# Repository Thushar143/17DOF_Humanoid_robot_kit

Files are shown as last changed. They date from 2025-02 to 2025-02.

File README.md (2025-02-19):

# README

## ROS2 Package

The `humanoid_description` ROS2 package was generated using the [`fusion2urdf-ros2`](https://github.com/dheena2k2/fusion2urdf-ros2) script.

### Important Notice
There are some errors in the script. Please ensure you rectify them as suggested [here](https://github.com/dheena2k2/fusion2urdf-ros2/pull/6/commits/3295ff1138d34191cdca01d7e633e04434cfb0c4) before running the Powershell commands to avoid issues in the package generation process.

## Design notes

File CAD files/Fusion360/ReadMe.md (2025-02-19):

# Important
## You should simplify the assembly before running the script.
To know how to simplify the assembly in Fusion refer to this [video](https://youtu.be/o7w7yv-Nros?t=3376).

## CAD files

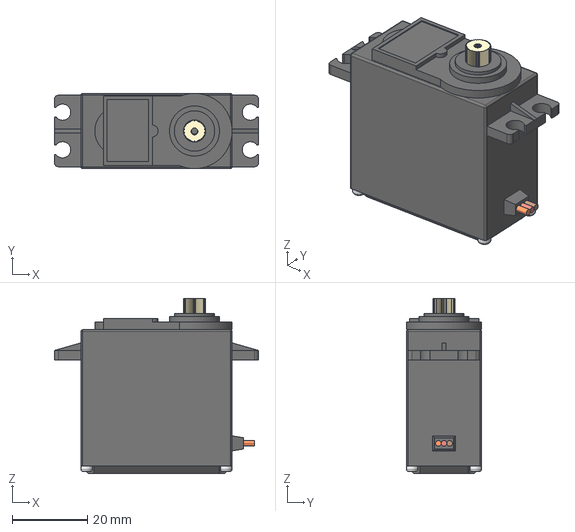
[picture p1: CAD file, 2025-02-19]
CAD files/Solidworks/MG996R.step
54.2 x 20.0 x 46.5 mm

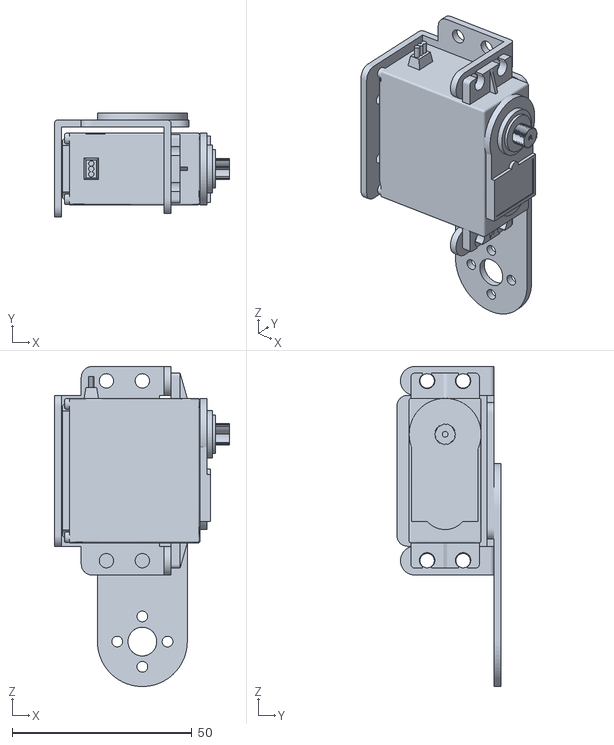
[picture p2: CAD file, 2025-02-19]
humanoid_description/meshes/L_forearm_1.stl
48.8 x 29.0 x 89.0

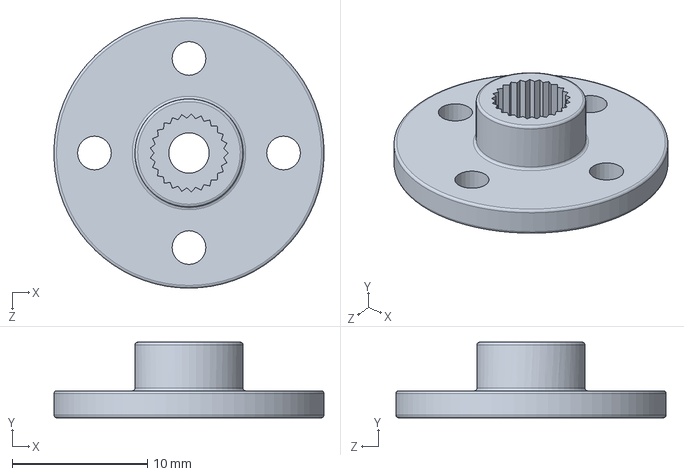
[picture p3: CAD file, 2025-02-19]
CAD files/Solidworks/Servo Mount - Horn Frame.SLDPRT
20.0 x 5.60 x 20.0 mm

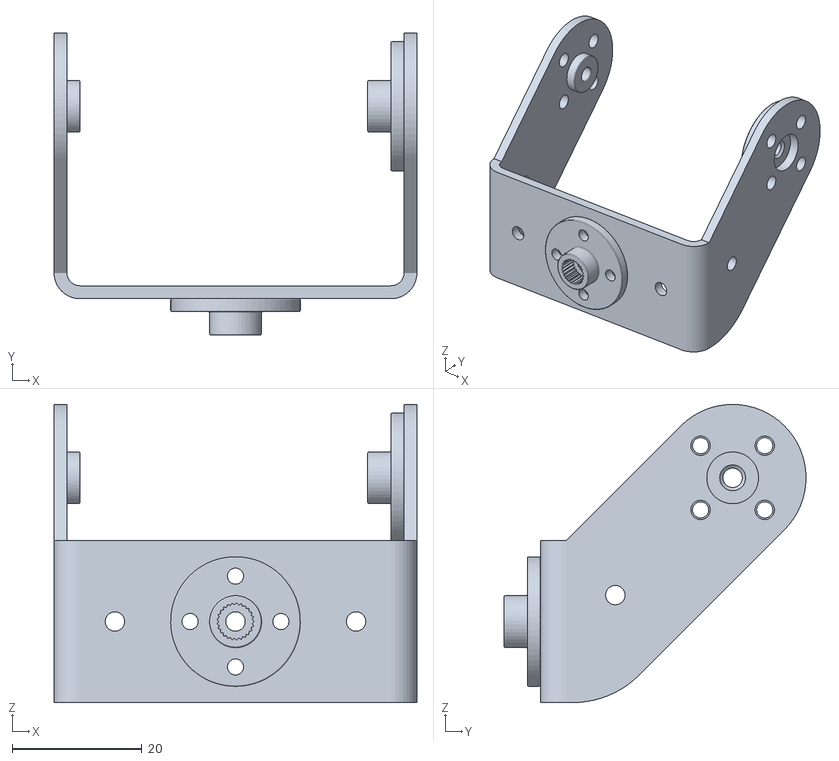
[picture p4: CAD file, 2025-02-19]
humanoid_description/meshes/L_shoulder_joint_1.stl
56.0 x 46.6 x 46.0

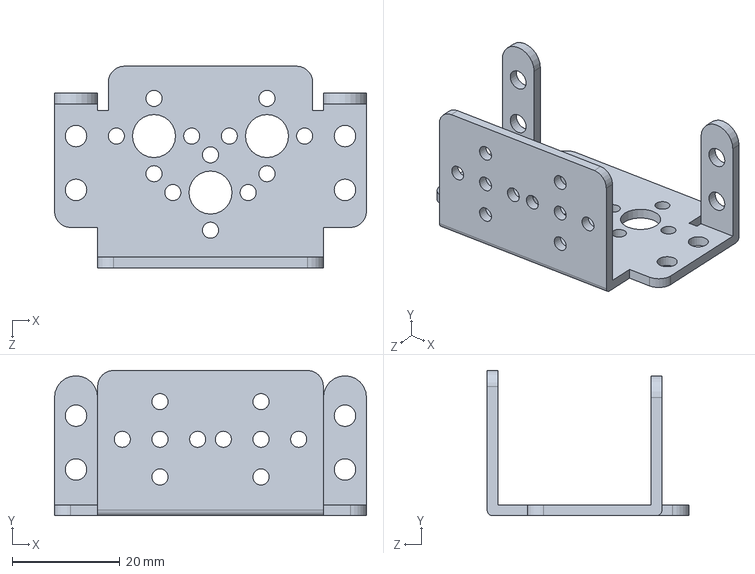
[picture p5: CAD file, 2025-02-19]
CAD files/Solidworks/servo motor mount.SLDPRT
58.0 x 27.0 x 37.5 mm

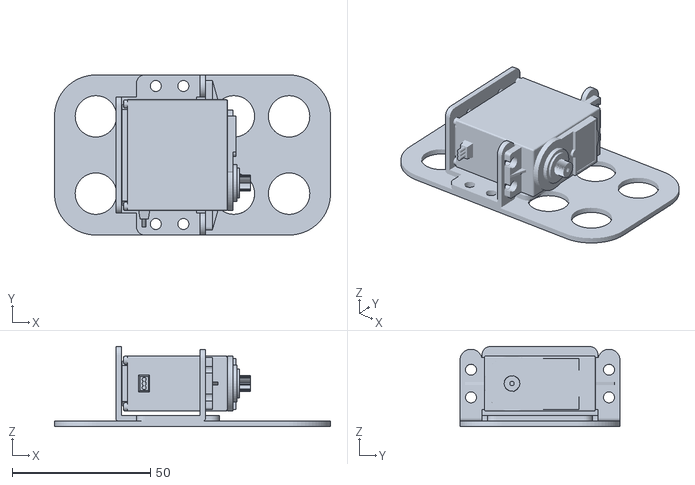
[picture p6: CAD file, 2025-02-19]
humanoid_description/meshes/L_ankle_roll_1.stl
100.0 x 58.0 x 29.0

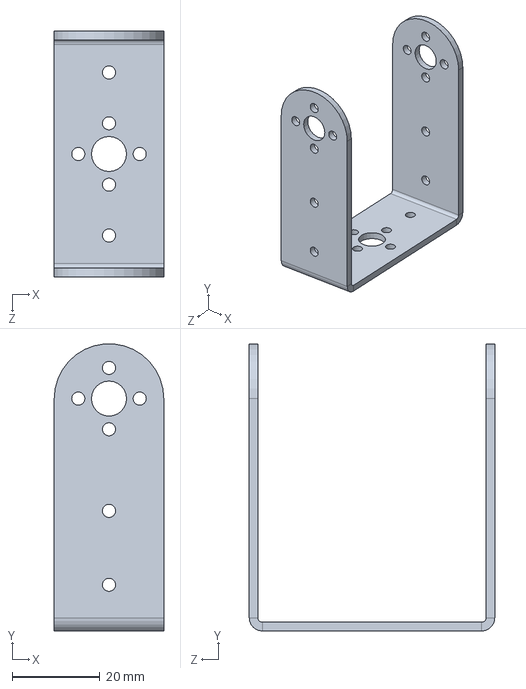
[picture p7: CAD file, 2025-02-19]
CAD files/Solidworks/Servo Bracket - U Shaped bis.SLDPRT
25.0 x 65.4 x 56.0 mm

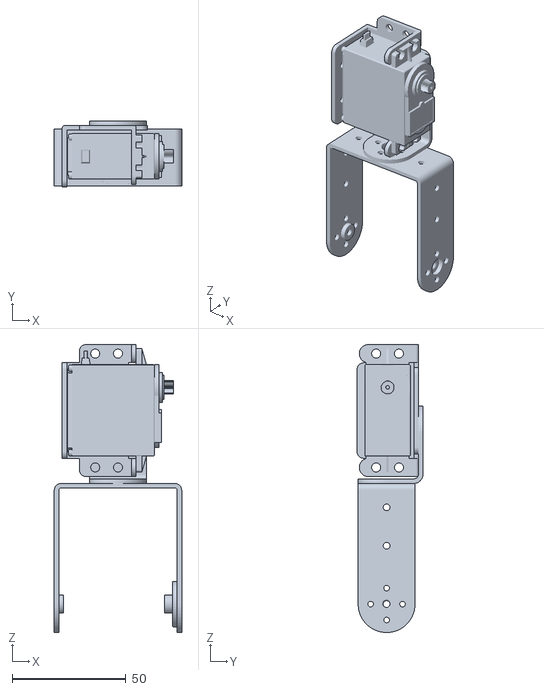
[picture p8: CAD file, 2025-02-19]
humanoid_description/meshes/L_upperarm_1.stl
56.0 x 29.0 x 126.5

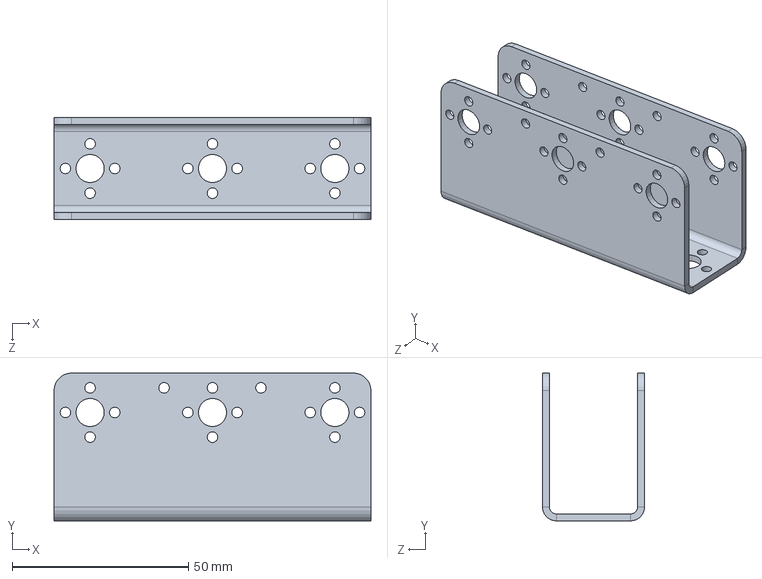
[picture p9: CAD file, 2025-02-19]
CAD files/Solidworks/Servo Bracket - Long U.SLDPRT
90.0 x 42.0 x 29.0 mm

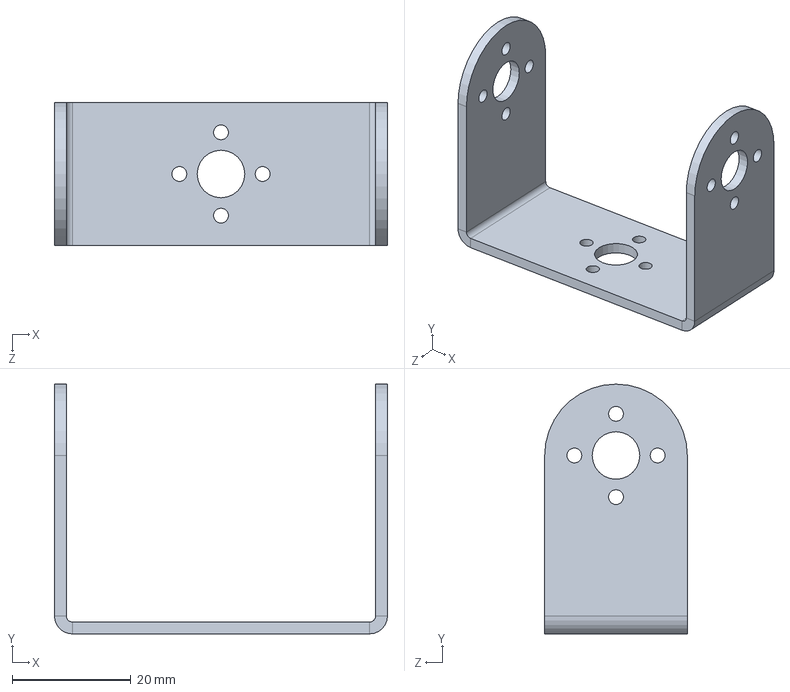
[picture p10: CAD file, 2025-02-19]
CAD files/Solidworks/U Bracket.SLDPRT
56.0 x 42.0 x 24.0 mm

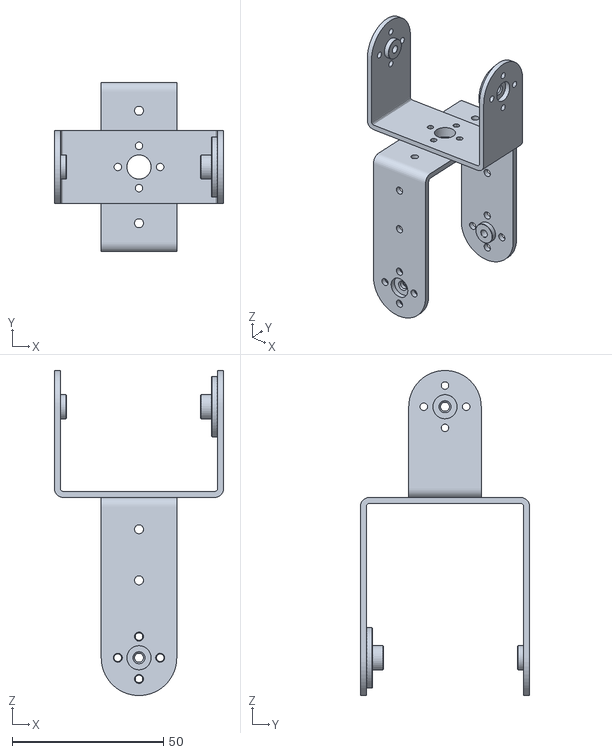
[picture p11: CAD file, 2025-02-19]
humanoid_description/meshes/R_hip_joint_1.stl
56.0 x 56.0 x 107.5

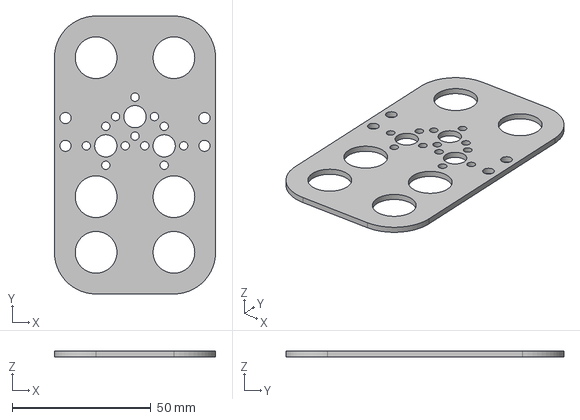
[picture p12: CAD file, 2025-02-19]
CAD files/Solidworks/newbase_plate.step
58.0 x 100.0 x 2.00 mm

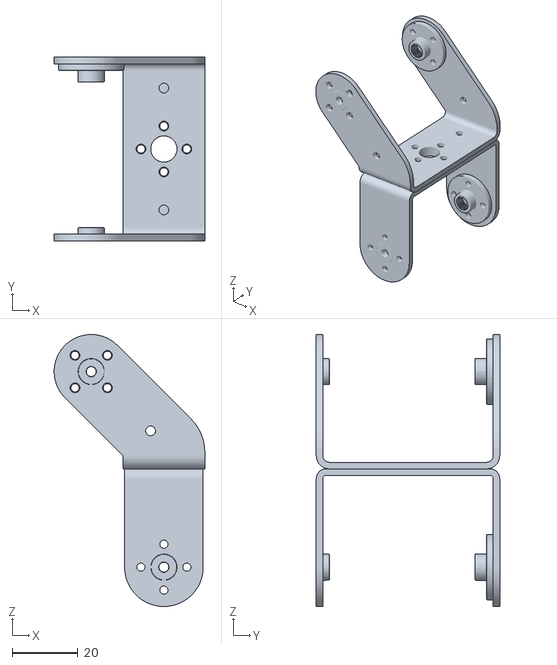
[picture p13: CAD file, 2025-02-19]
humanoid_description/meshes/L_knee_1.stl
46.0 x 56.0 x 83.0

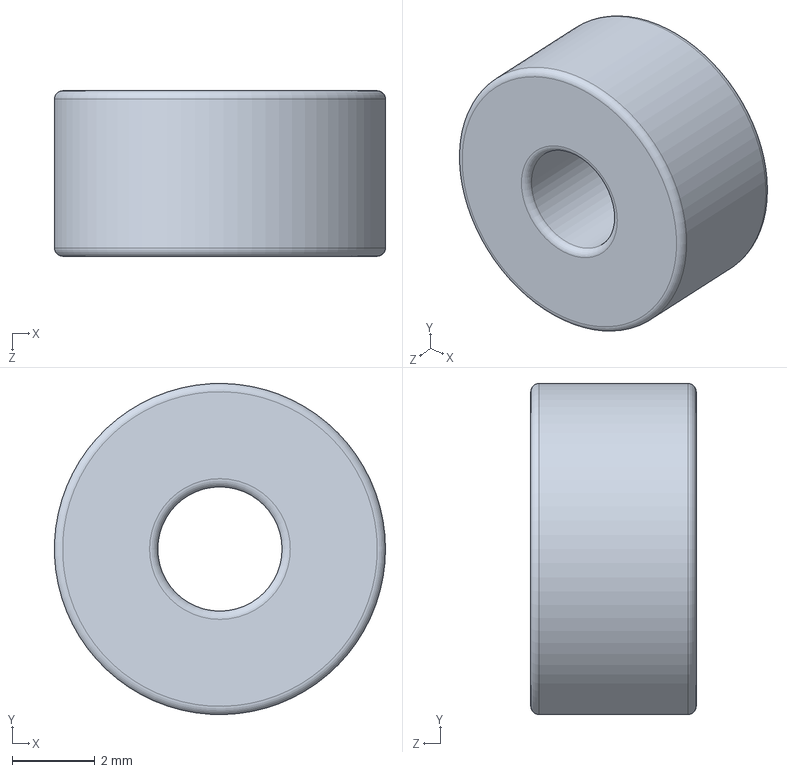
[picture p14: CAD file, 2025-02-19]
CAD files/Solidworks/3x8x4 mm radial ball bearing.SLDPRT
8.00 x 8.00 x 4.00 mm

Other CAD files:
humanoid_description/meshes/R_forearm_1.stl
humanoid_description/meshes/base_link.stl
CAD files/Solidworks/Servo Bracket - U Shaped inclined.SLDPRT
humanoid_description/meshes/R_knee_1.stl
CAD files/Fusion360/Robot assembly.f3z
CAD files/Solidworks/Flat Bracket.SLDPRT
CAD files/Solidworks/Servo Bracket - Corner Mount.SLDPRT
humanoid_description/meshes/Head_1.stl
humanoid_description/meshes/L_ankle_pitch_1.stl
humanoid_description/meshes/L_hip_joint_1.stl
humanoid_description/meshes/L_thigh_1.stl
humanoid_description/meshes/R_ankle_pitch_1.stl
humanoid_description/meshes/R_ankle_roll_1.stl
humanoid_description/meshes/R_shoulder_joint_1.stl
humanoid_description/meshes/R_thigh_1.stl
humanoid_description/meshes/R_upperarm_1.stl

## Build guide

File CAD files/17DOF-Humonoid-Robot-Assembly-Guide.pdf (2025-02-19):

### Overview:

17 DOF Humanoid Robot from Robu.in comes with 17 degrees of freedom joints. Its actuated using
17 Metal Gear Standard Servo (or) Servo Economy. This Humanoid Robot is controlled by ARDUINO UNO R3 BASED USB 18 SERVO CONTROLLER (Optionally available with Bluetooth). It can also be controlled by PC using USB 18 Servo Controller Software. The software helps to develop the complex sequences in real time on the hardware. It also generates Arduino based code for the developed sequence which can be deployed on the controller on board thereby making the robot autonomous.

The power requirement for this robot is 5 to 6V DC 10 Amp power supply. It could be either battery or a AC power supply rated at 5-6VDC. You can also use a modified computer SMPS supply, it is available for sale on Robu.in website. The detailed features of the Servo Controller are:

- Control 18 hobby servos from PC and Microcontroller
- USB interface
- Comes Pre-loaded Arduino Uno bootloader
- Software exports servo sequences to Arduino Uno for running servo sequences
- Independent range setting for each servo
- Independent offset, Maximum, Minimum and Direction setting for each servo
- 0.5-microsecond resolution
- 50 Hz update rate
- Small size of 80 X 47 mm
- Plug and Play, Auto detection of hardware
- Easy to use software
- Servo sequencer with speed, delay, goto and many other features
- Home and neutral position setting
- Easy to install USB driver and Application software
- Bluetooth interface for wireless control of robots (Optionally available)

After assembling the Humanoid Robot you will be able to control it from a Windows PC. You can also develop your own sequences in real time on hardware and can generate the code for Arduino which will be deployed onto the board making robot autonomous.

Let’s start with the basic assembly of Humanoid Robot. Some basic tools like screw drivers, pliers, small spanners, soldering iron, wire cutter, nipper, stripper are required to complete the assembly.

The notations used in this document for screws, nuts, bolts and other parts are like these:

1. M4 x 12 Screw - M4 Screw
2. M4 x 12 Screw Nut - M4 Nut
3. 3 x 6 Servo Screw - Servo Screw
4. Miniature Ball Radial Bearing - Bearing
5. 3 mm Nylock Nut - Lock nut
6. 3 mm Nut - Nut
7. 3 x 6 Button Head Screw - Small Button Screw
8. 3 x 10 Button Head Screw - Big Button Screw
9. 3 x 6 CSK Screw - CSK Screw
10. M3 x 8 Screw - M3 Mid Screw
11. Metal Horn for Servo 25T - Servo Horn
12. Metal Gear Standard Servo (or) Servo Economy - Servo Motor
13. Multipurpose Aluminium Standard Servo Bracket - Multipurpose Bracket
14. Short U Shape Aluminium Servo Bracket - Short U Bracket
15. Long U Aluminium Servo Bracket - Long U Bracket
16. Oblique U Shape Aluminium Servo Bracket - Oblique U Bracket
17. Interconnect Aluminium Servo Bracket - Interconnect Bracket
18. L Shaped Interconnect Servo Bracket - L Shaped Bracket
19. Large U Beam Aluminium Servo Bracket - Large U Bracket
20. Robot feet Aluminium Servo Bracket - Robot Feet

### Steps to Assemble Humanoid Robot:

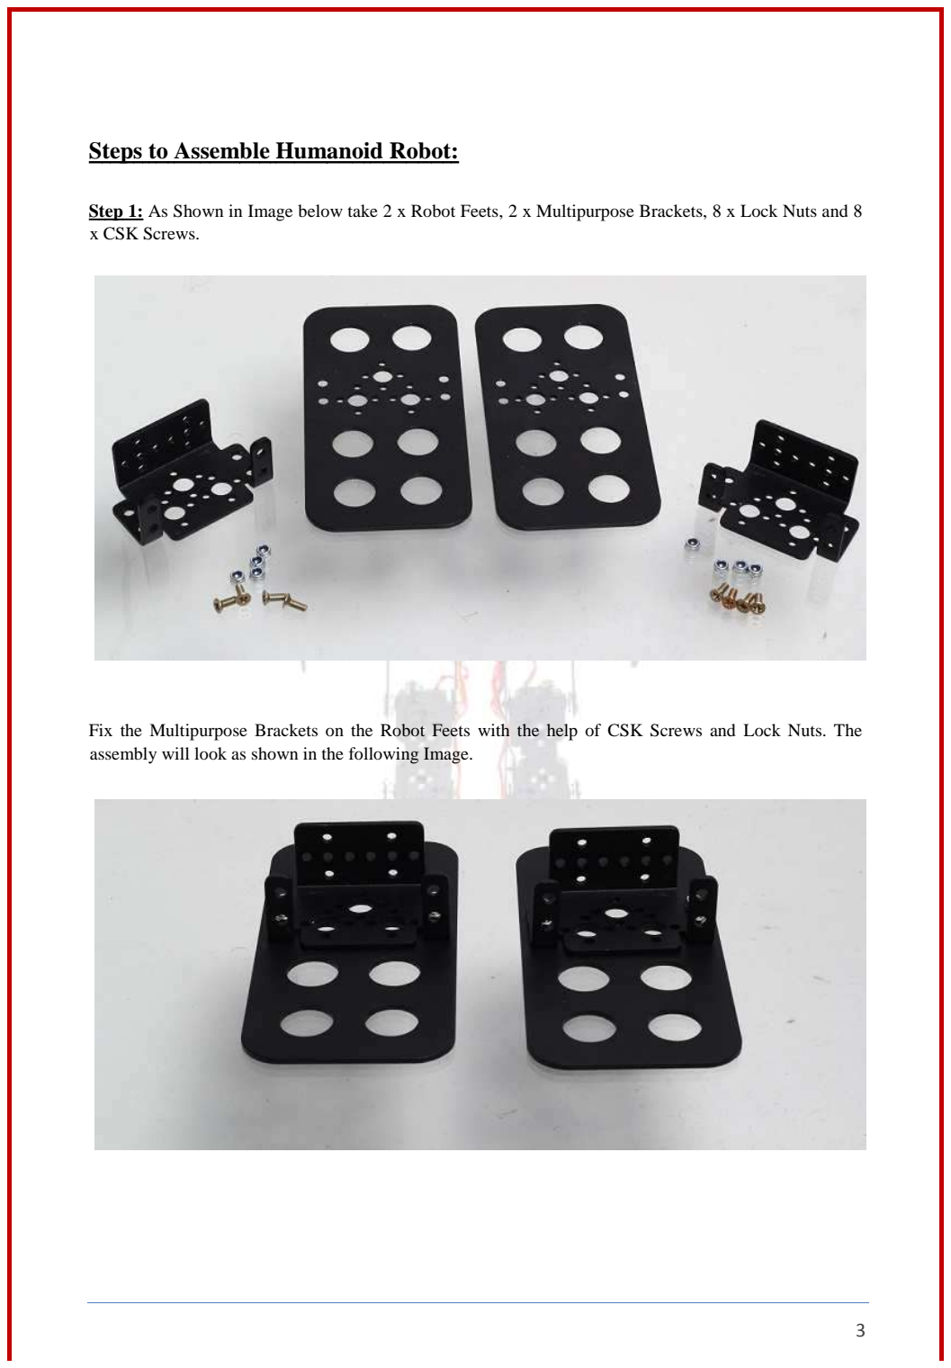
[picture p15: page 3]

Step 1: As Shown in Image below take 2 x Robot Feets, 2 x Multipurpose Brackets, 8 x Lock Nuts and 8 x CSK Screws.

Fix the Multipurpose Brackets on the Robot Feets with the help of CSK Screws and Lock Nuts. The assembly will look as shown in the following Image.

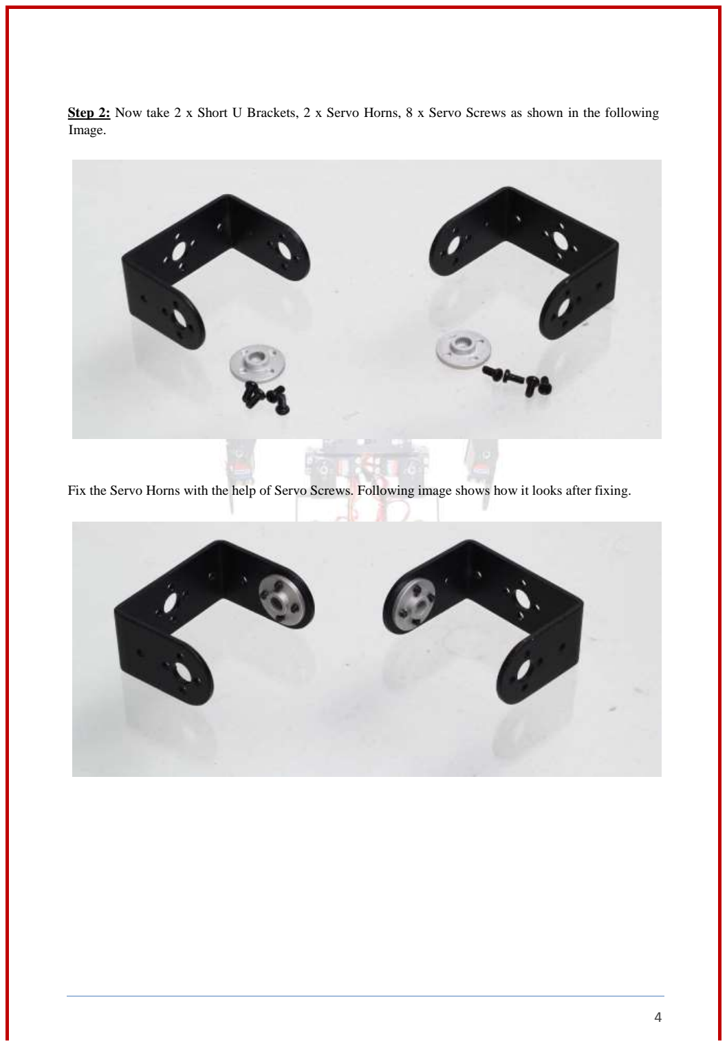
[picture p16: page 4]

Step 2: Now take 2 x Short U Brackets, 2 x Servo Horns, 8 x Servo Screws as shown in the following Image.

Fix the Servo Horns with the help of Servo Screws. Following image shows how it looks after fixing.

Step 3: Fix the Short U Brackets on the Multipurpose Brackets as shown in following image by using 2 x M3 Mid Screws, 2 x Lock Nuts, and 2 x Bearings shown in the Black Boxes in below image.

Step 4: Now take 2 x Servo Motors, 8 x M4 Screws and 8 x M4 Nuts as shown below.

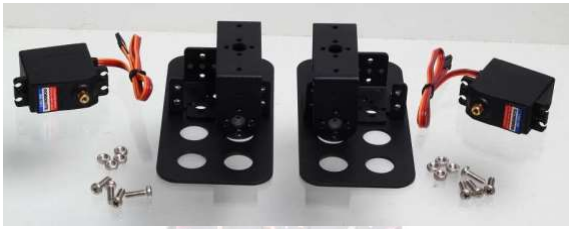
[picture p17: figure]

Fix the Servo Motors in the assembly as shown below with the help of M4 Mid Screws and M4 Nuts. Now the Black Box in the below image shows the Servo Screw which is to be fixed to Servo Motor Shaft after Neutralizing the Servo Motor. To Neutralize connect the Servo Motor to Servo Controller. Power up Servo Controller with 5 to 6 VDC power supply and connect to PC software with USB or Bluetooth connection. Neutralize the servo (Put the servo to center position) using software. After that tight the Servo Screw (Shown in Black Box) to the Shaft of the Servo Motor as shown in the below image.

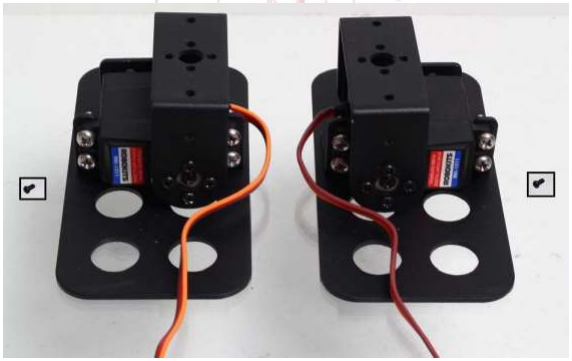
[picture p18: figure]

Step 5: Now take 2 x Multipurpose Brackets, 8 x Big Button Screws, and 8 x Lock Nuts.

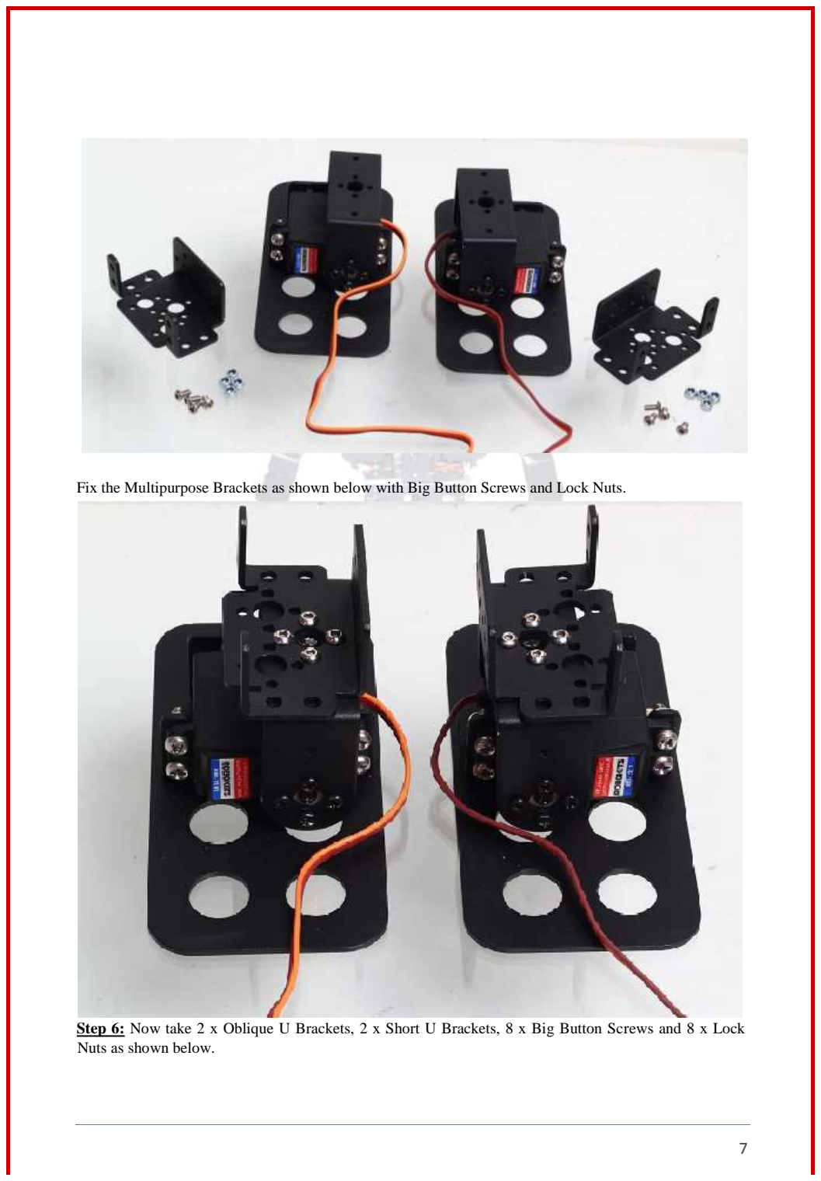
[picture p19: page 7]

Fix the Multipurpose Brackets as shown below with Big Button Screws and Lock Nuts.

Step 6: Now take 2 x Oblique U Brackets, 2 x Short U Brackets, 8 x Big Button Screws and 8 x Lock Nuts as shown below.

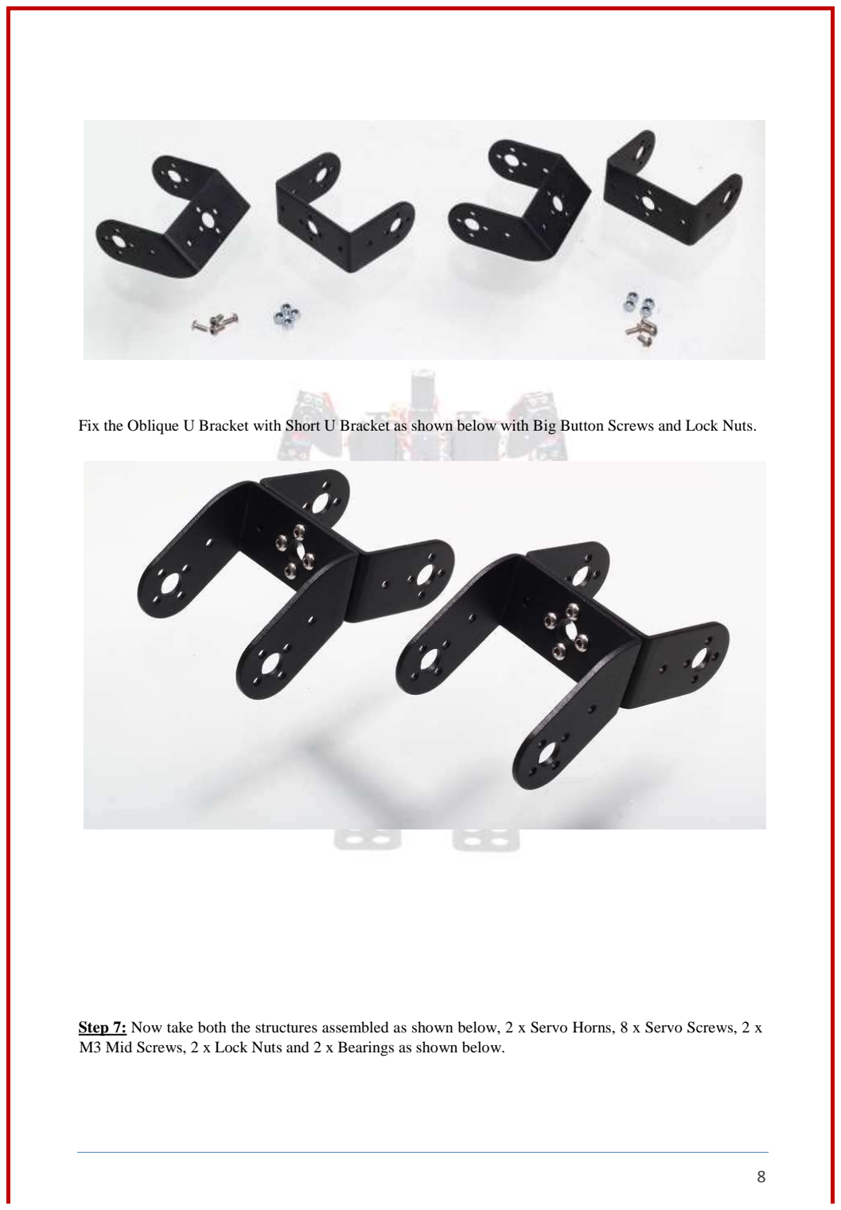
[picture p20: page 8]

Fix the Oblique U Bracket with Short U Bracket as shown below with Big Button Screws and Lock Nuts.

Step 7: Now take both the structures assembled as shown below, 2 x Servo Horns, 8 x Servo Screws, 2 x M3 Mid Screws, 2 x Lock Nuts and 2 x Bearings as shown below.

Assemble the structure as shown in the following image.

Step 8: Now take 2 x Servo Motors, 8 x M4 Screws, 8 x M4 Nuts and the structure assembled in previous step. This Servos are to be fixed on the Multipurpose Brackets seen in the following image.

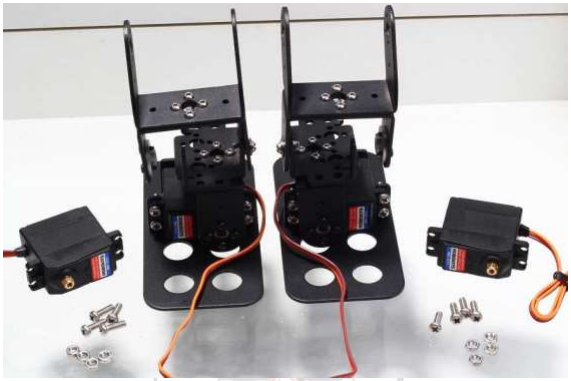
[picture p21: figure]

Fix the Servo Motor on the Multipurpose Brackets as seen in the below image. Neutralize the Motor and then tight the Servo Screw on the Motor Shaft. The Servo Screws are shown in the Black Boxes.

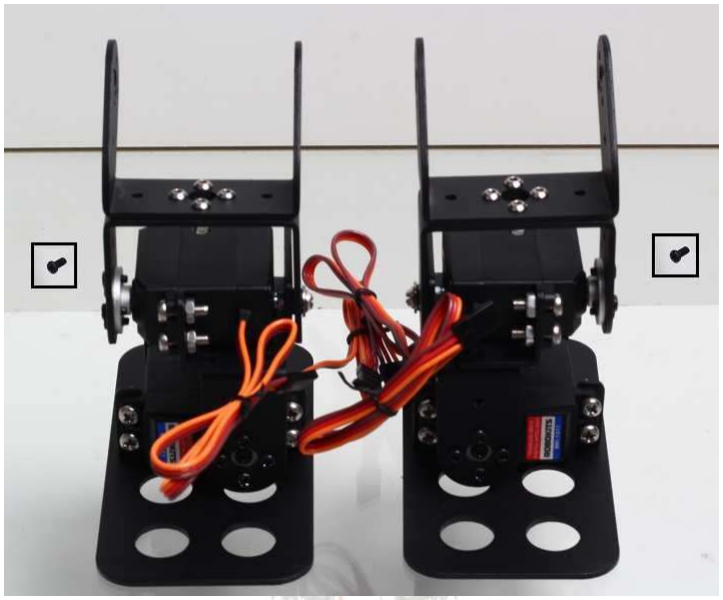
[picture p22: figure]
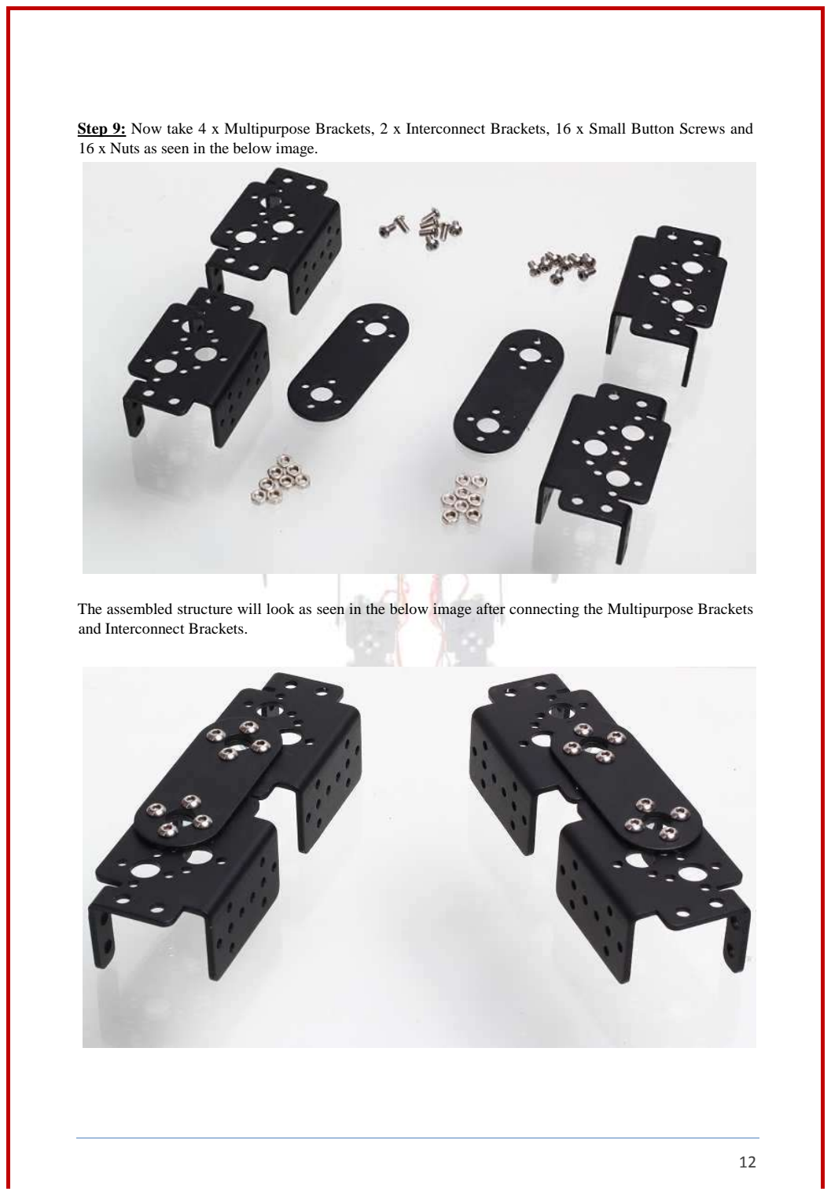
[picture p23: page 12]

Step 9: Now take 4 x Multipurpose Brackets, 2 x Interconnect Brackets, 16 x Small Button Screws and 16 x Nuts as seen in the below image.

The assembled structure will look as seen in the below image after connecting the Multipurpose Brackets and Interconnect Brackets.

Step 10: The following image shows the two structures that we have assembled. To connect both of them we need 2 x M3 Mid Screws, 2 x Lock Nuts (image shows nuts but you can use Lock Nuts), 2 x Bearings. Also we need 8 x Servo Screws and 2 x Servo Horns for further assembly.

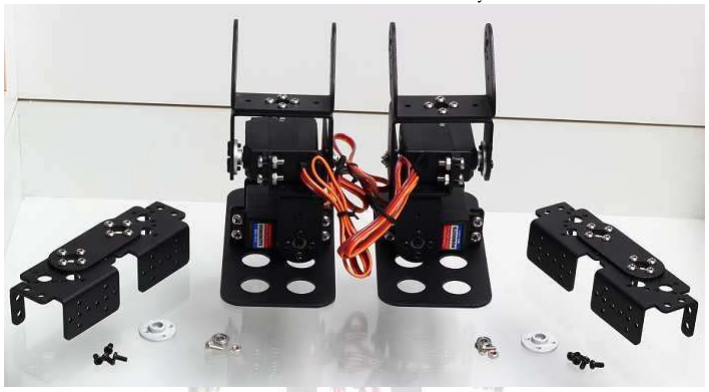
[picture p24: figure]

Fix the both the structures as seen in the below image with the help of M3 Mid Screws, Nuts and Bearings.
Also fix the Servo Horns.

Step 11: Now take 2 x Long U Brackets, 2 x Servo Horns, 8 x Servo Screws, 2 x M3 Mid Screws, 2 x Lock Nuts and 2 x Bearings as seen the below image along with the assembled structure.

Fix the Long U Brackets to the Structure as seen in the below image with the help of M3 Mid Screws and Lock Nuts. Also fix the Servo Horns.

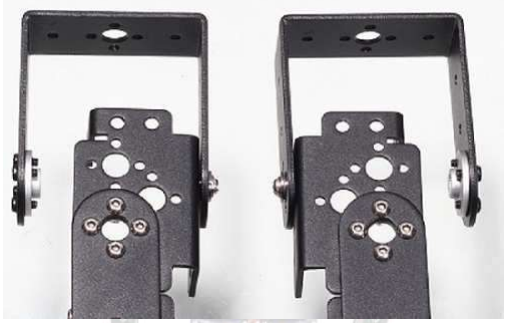
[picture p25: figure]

Step 12: Now take 4 x Servo Motors, 16 x M4 Screws, 16 x M4 Nuts, 4 x Servo Screws. Fix the Servo Motors at Place 1, 2, 3 and 4 shown in the Red Color in the below image. Tight the Servo Screws to the shaft of each Servo Motor after neutralizing each Servo Motor. The following image shows the Servo Motors already fixed.

The M4 Screws, M4 Nuts and the Servo Motor is shown below in the Big Black Box while the Servo Screw is shown in the small Black Box.

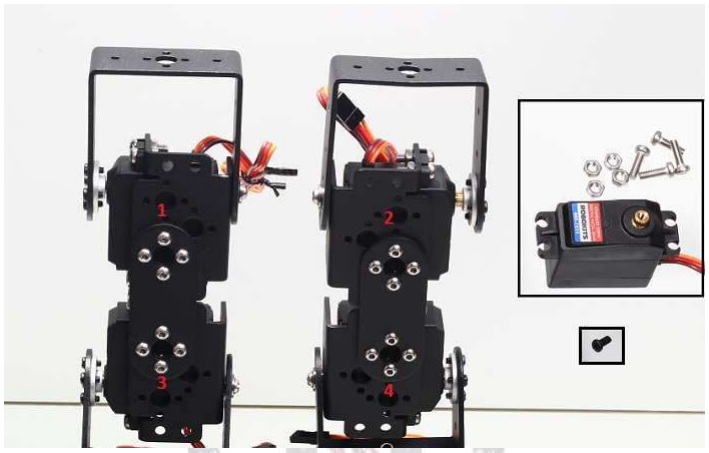
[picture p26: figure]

Step 13: Take 2 x Short U Brackets, 8 x Big Button Screws and 8 x Lock Nuts. Fix the Short U Brackets on the top of Long U Brackets with the help of Big Button Screws and Lock Nuts. The structure after fixing the Short U Brackets is shown in the main image below. The Short U Brackets, Big Button Screws and Lock Nuts is shown in the Black Box in the below image.

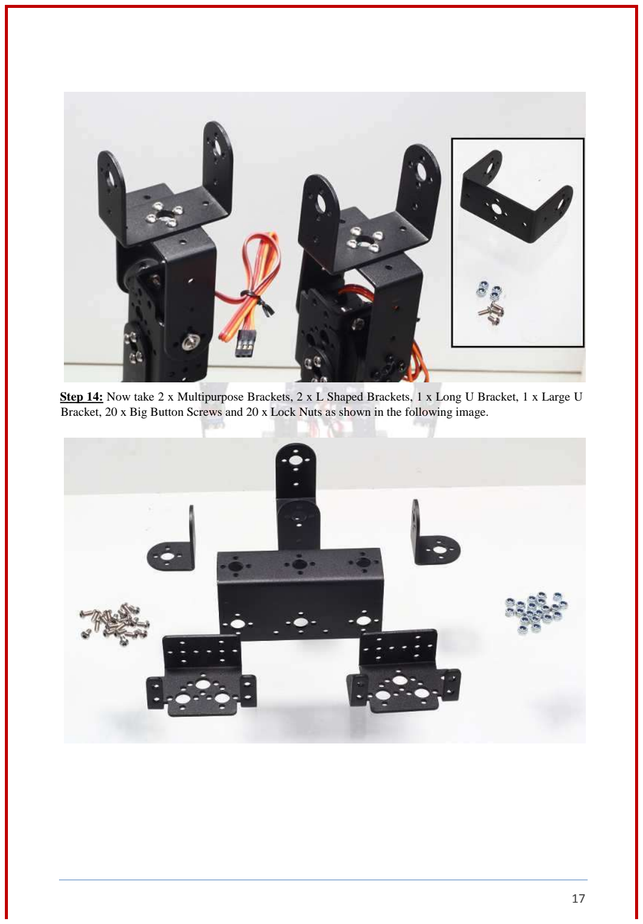
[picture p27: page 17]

Step 14: Now take 2 x Multipurpose Brackets, 2 x L Shaped Brackets, 1 x Long U Bracket, 1 x Large U Bracket, 20 x Big Button Screws and 20 x Lock Nuts as shown in the following image.

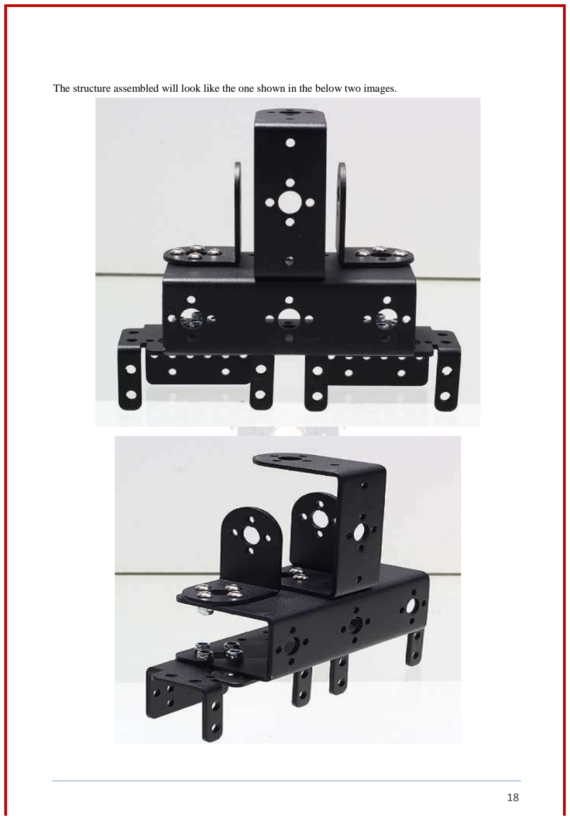
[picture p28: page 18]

The structure assembled will look like the one shown in the below two images.

Step 15: Now we will connect the two structures that we have already assembled in previous steps and they are also shown below. To connect them take 2 x M3 Mid Screws, 2 x Lock Nuts and 2 x Bearings. Also take 2 x Servo Horns and 8 x Servo Screws for fixing the Servo Motors.

After connecting the two structures the assembly will look as shown in the following image.

Step 16: Now take 2 x Servo Motors, 8 x M4 Screws, 8 x M4 Nuts and 2 x Servo Screws. The Servo Motors are to be fixed at place 1 and 2 shown in the below image.

The Servo Screws is to be fixed at the shaft of both Servo Motors after neutralizing the Servo Motors.

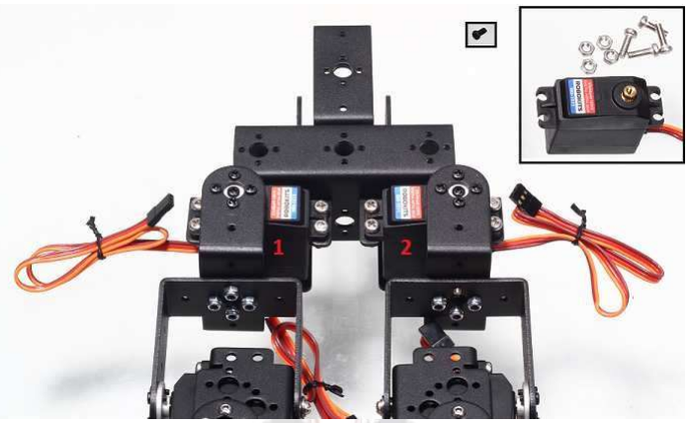
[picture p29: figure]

Step 17: Now take 2 x Multipurpose Brackets, 8 x Big Button Screws and 8 x Lock Nuts which are shown in the Black Box in the following image.

These Multipurpose Brackets are to be fixed at the places 1 and 2 Shown in the below image with the help of Screws and Nuts taken.

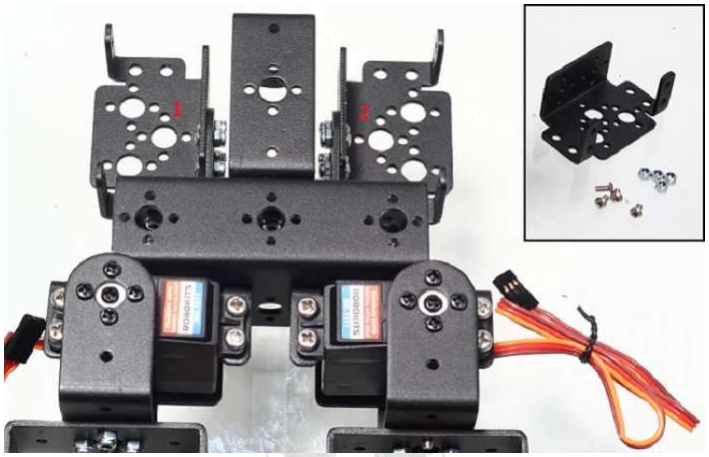
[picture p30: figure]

Step 18: Now take 2 x Servo Motors, 8 x M4 Screws and 8 x M4 Nuts and fix them at place 1 and 2.

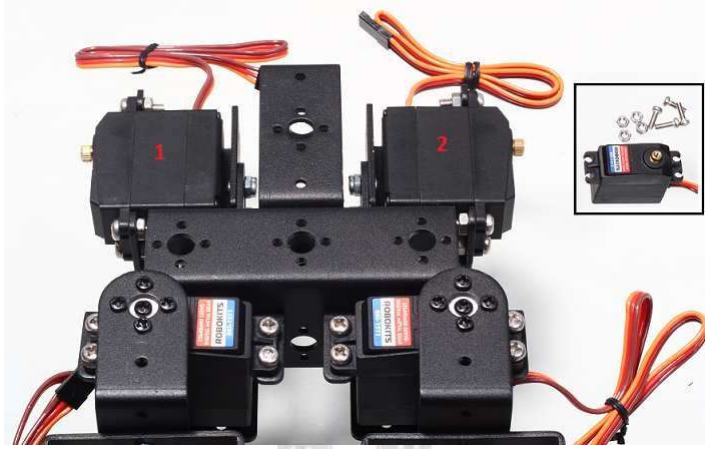
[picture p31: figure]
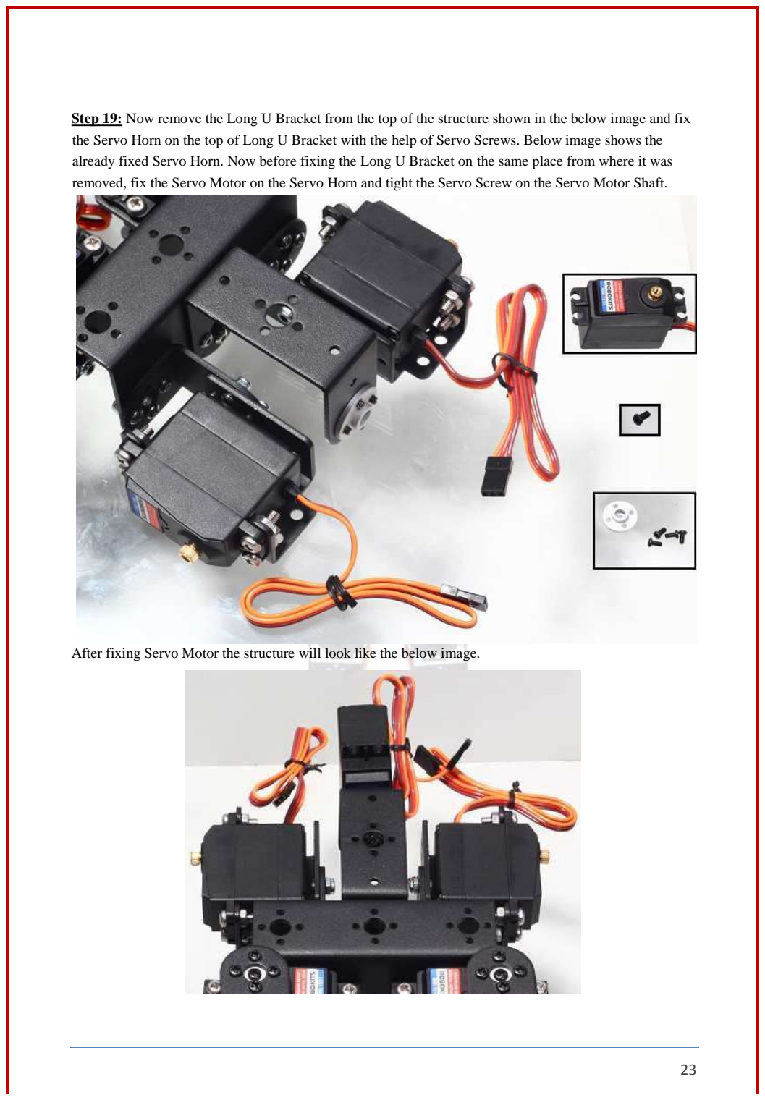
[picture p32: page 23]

Step 19: Now remove the Long U Bracket from the top of the structure shown in the below image and fix the Servo Horn on the top of Long U Bracket with the help of Servo Screws. Below image shows the already fixed Servo Horn. Now before fixing the Long U Bracket on the same place from where it was removed, fix the Servo Motor on the Servo Horn and tight the Servo Screw on the Servo Motor Shaft.

After fixing Servo Motor the structure will look like the below image.

Step 20: Now let’s assemble both the hands of Humanoid Robot. Take 2 x Oblique U Brackets, 2 x Multipurpose Brackets, 2 x Servo Horns, 8 x Servo Screws, 2 x M3 Mid Screws, 2 x Lock Nuts and 2 x Bearings. Below sequence of images shows the assembly.

After doing so you will get two structures shown below one for Right Hand and another for Left Hand.

Step 21: Now take the two structures assembled in previous step along with 2 x L Shaped Brackets, 2 x Servo Horns, 8 x Servo Screws, 8 Small Button Screws, and 8 Nuts as shown in the below image.

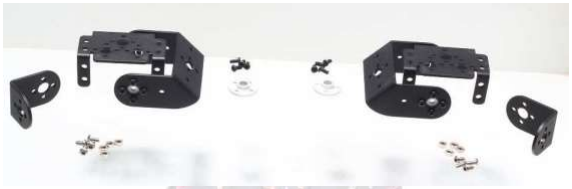
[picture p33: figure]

Now after fixing the Servo Horns and L Shaped Brackets you will have the following two structures.

Step 22: Now take 2 x Long U Brackets, 8 x Small Button Screws, 8 x Nuts along with already assembled structures as shown in following Image.

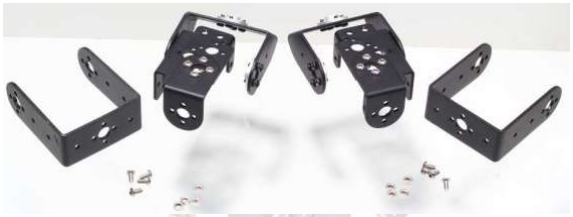
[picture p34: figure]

After fixing Long U Brackets you will have the below structures.

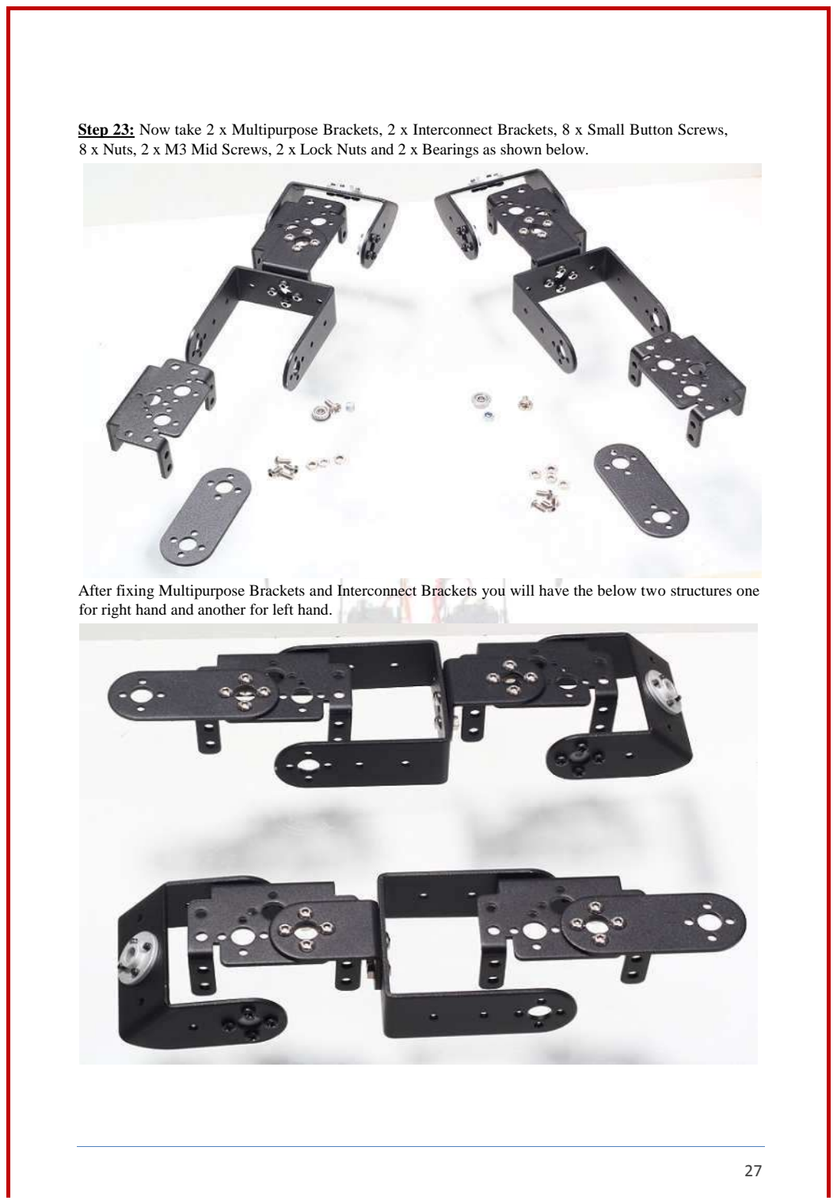
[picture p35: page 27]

Step 23: Now take 2 x Multipurpose Brackets, 2 x Interconnect Brackets, 8 x Small Button Screws, 8 x Nuts, 2 x M3 Mid Screws, 2 x Lock Nuts and 2 x Bearings as shown below.

After fixing Multipurpose Brackets and Interconnect Brackets you will have the below two structures one for right hand and another for left hand.

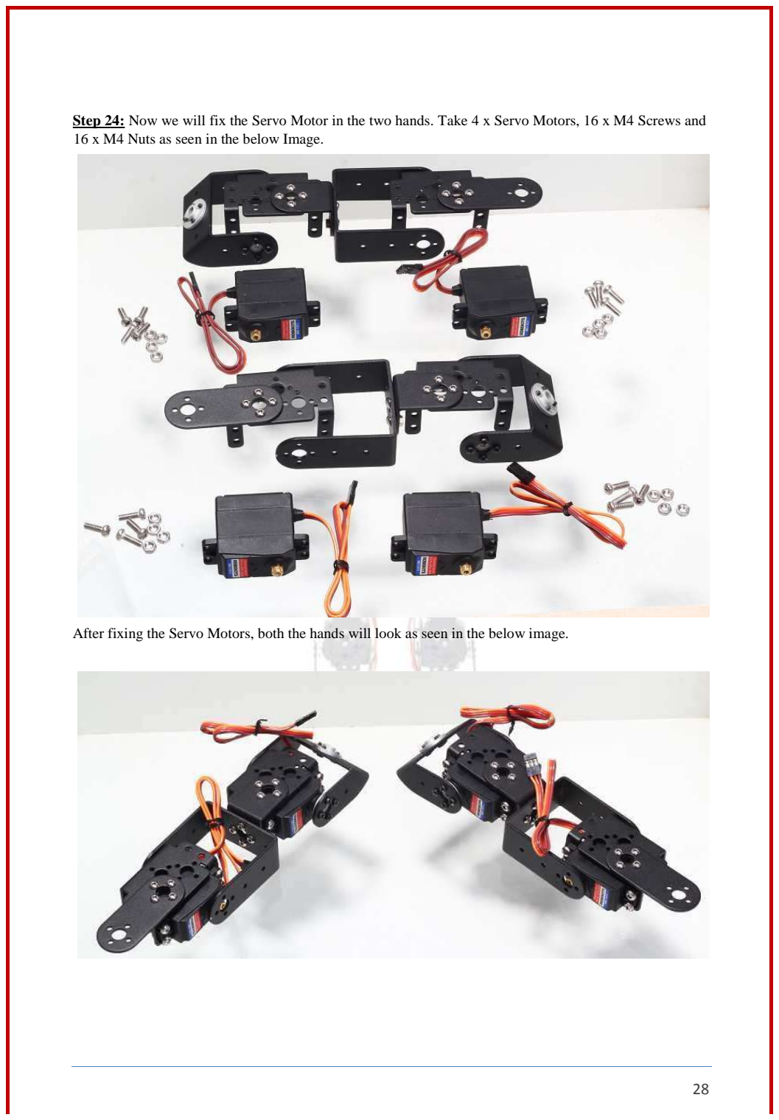
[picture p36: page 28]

Step 24: Now we will fix the Servo Motor in the two hands. Take 4 x Servo Motors, 16 x M4 Screws and 16 x M4 Nuts as seen in the below Image.

After fixing the Servo Motors, both the hands will look as seen in the below image.

Step 25: Now take 2 x Servo Horns and 8 x Servo Screws to fix the Servo Horns for the last two Servo Motors.

After fixing the Servo Motors neutralize all the four Motors and tight the Servo Horns Screws shown in the Small Black Box on the Shaft of all the Servo Motors.

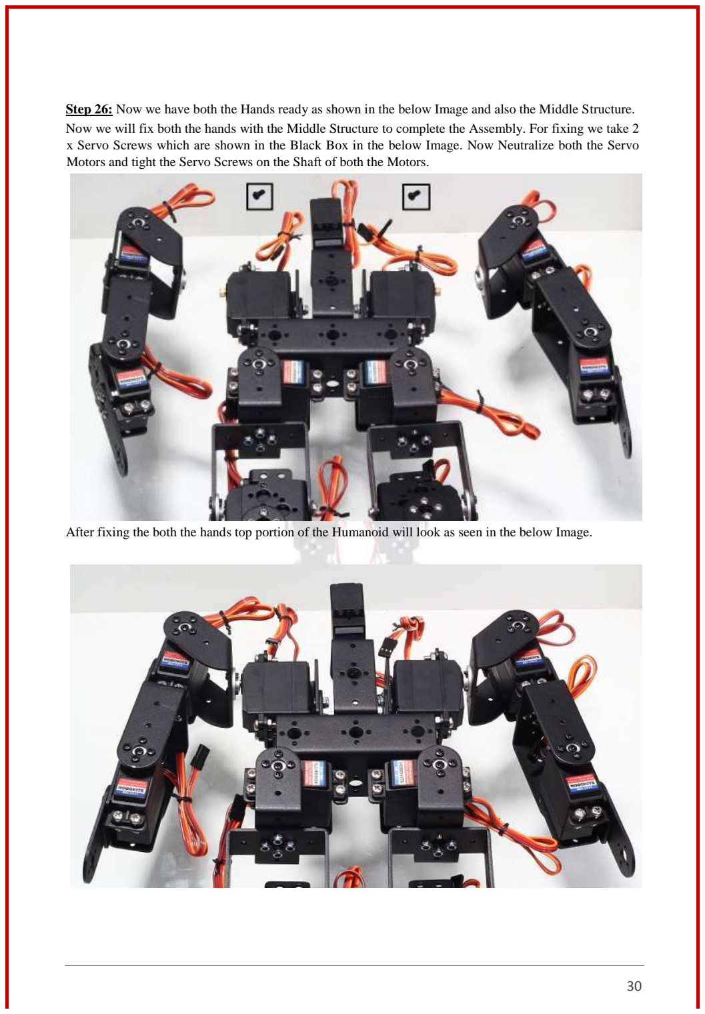
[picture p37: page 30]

Step 26: Now we have both the Hands ready as shown in the below Image and also the Middle Structure. Now we will fix both the hands with the Middle Structure to complete the Assembly. For fixing we take 2 x Servo Screws which are shown in the Black Box in the below Image. Now Neutralize both the Servo Motors and tight the Servo Screws on the Shaft of both the Motors.

After fixing the both the hands top portion of the Humanoid will look as seen in the below Image.

Following all the above steps assembly of the Humanoid Robot will complete and Humanoid Robot will look as below:

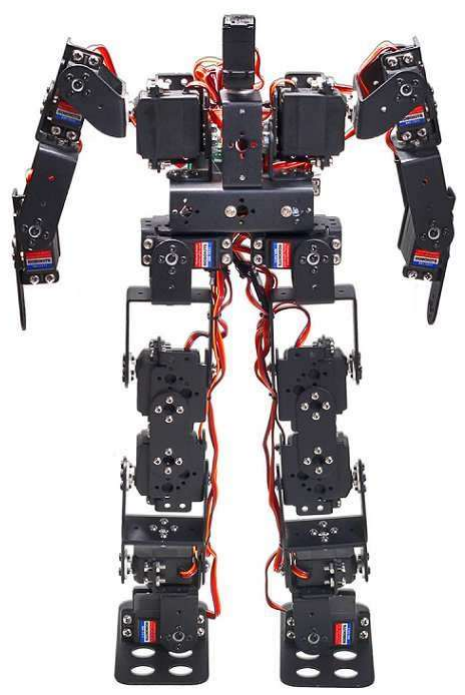
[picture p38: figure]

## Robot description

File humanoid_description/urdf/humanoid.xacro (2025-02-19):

<?xml version="1.0" ?>
<robot name="humanoid" xmlns:xacro="http://www.ros.org/wiki/xacro">

<xacro:include filename="$(find humanoid_description)/urdf/materials.xacro" />
<xacro:include filename="$(find humanoid_description)/urdf/humanoid.trans" />
<xacro:include filename="$(find humanoid_description)/urdf/humanoid.gazebo" />
<link name="base_link">
  <inertial>
    <origin xyz="-0.012883479435964856 -0.0022883102773944906 0.3195103923670224" rpy="0 0 0"/>
    <mass value="0.49620714060674026"/>
    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
  </inertial>
  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
</link>

<link name="L_hip_joint_1">
  <inertial>
    <origin xyz="0.02476294562748635 0.0007629287180515379 -0.03845870411401925" rpy="0 0 0"/>
    <mass value="0.043964600871803455"/>
    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
  </inertial>
  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
</link>

<link name="L_thigh_1">
  <inertial>
    <origin xyz="0.0020631851599692396 0.021610549494278094 -0.03835026650914522" rpy="0 0 0"/>
    <mass value="0.6278799138265152"/>
    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
  </inertial>
  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
</link>

<link name="L_knee_1">
  <inertial>
    <origin xyz="0.01778979357133356 0.02573859555380659 -0.029178246058454205" rpy="0 0 0"/>
    <mass value="0.03721244648561897"/>
    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
  </inertial>
  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
</link>

<link name="L_ankle_pitch_1">
  <inertial>
    <origin xyz="-0.008957916317498007 0.020419475919971005 -0.005543744818484048" rpy="0 0 0"/>
    <mass value="0.3560292146171612"/>
    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
  </inertial>
  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
</link>

<link name="L_ankle_roll_1">
  <inertial>
    <origin xyz="0.022510537177657726 0.009228652532095816 -0.00407575705258406" rpy="0 0 0"/>
    <mass value="0.37095119393642895"/>
    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
  </inertial>
  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
</link>

<link name="R_hip_joint_1">
  <inertial>
    <origin xyz="0.024762945627578324 -0.000762795394638742 -0.03845870411416624" rpy="0 0 0"/>
    <mass value="0.1224728167143094"/>
    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
  </inertial>
  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
</link>

<link name="R_thigh_1">
  <inertial>
    <origin xyz="0.002063185159969369 -0.021610415517168198 -0.03843242882065484" rpy="0 0 0"/>
    <mass value="0.6278799138265153"/>
    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
  </inertial>
  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
</link>

<link name="R_knee_1">
  <inertial>
    <origin xyz="0.017789793571273534 -0.02573846223038475 -0.029178246058392504" rpy="0 0 0"/>
    <mass value="0.03859068524434563"/>
    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
  </inertial>
  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
</link>

<link name="R_ankle_pitch_1">
  <inertial>
    <origin xyz="-0.008957916317495346 -0.020419342902477204 -0.005539333272074516" rpy="0 0 0"/>
    <mass value="0.35602921461716464"/>
    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
  </inertial>
  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
</link>

<link name="R_ankle_roll_1">
  <inertial>
    <origin xyz="0.022510537177669827 -0.009228518658190743 -0.004076152987495269" rpy="0 0 0"/>
    <mass value="0.3709511939353679"/>
    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
  </inertial>
  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
</link>

<link name="L_shoulder_joint_1">
  <inertial>
    <origin xyz="0.0015299174878798602 0.01478285543107169 0.007715270715101474" rpy="0 0 0"/>
    <mass value="0.021144305664436213"/>
    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
  </inertial>
  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
</link>

<link name="L_upperarm_1">
  <inertial>
    <origin xyz="0.022436519365852024 0.0017478415011937254 -0.02062009535457715" rpy="0 0 0"/>
    <mass value="0.39400171797745537"/>
    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
  </inertial>
  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
</link>

<link name="L_forearm_1">
  <inertial>
    <origin xyz="0.021698764719735014 0.0024589629396612606 -0.010974756579181455" rpy="0 0 0"/>
    <mass value="0.3238214913391936"/>
    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
  </inertial>
  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
</link>

<link name="R_shoulder_joint_1">
  <inertial>
    <origin xyz="0.001530575565089766 -0.014783722107877845 0.007715270714952593" rpy="0 0 0"/>
    <mass value="0.021144305664436244"/>
    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
  </inertial>
  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
</link>

<link name="R_upperarm_1">
  <inertial>
    <origin xyz="0.022437177458494186 -0.0017516937321476328 -0.020620095395556093" rpy="0 0 0"/>
    <mass value="0.39400171893460806"/>
    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
  </inertial>
  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
</link>

<link name="R_forearm_1">
  <inertial>
    <origin xyz="0.02169942279604719 -0.0024636789234836892 -0.010974756579181955" rpy="0 0 0"/>
    <mass value="0.32382149133918564"/>
    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
  </inertial>
  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
</link>

<link name="Head_1">
  <inertial>
    <origin xyz="0.009916301072321384 2.611393220511727e-06 0.02595144565080304" rpy="0 0 0"/>
    <mass value="0.2579403843929263"/>
    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
  </inertial>
  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
</link>

<joint name="L_hip_joint" type="revolute">
  <origin xyz="-0.03132 0.041871 0.280792" rpy="0 0 0"/>
  <parent link="base_link"/>
  <child link="L_hip_joint_1"/>
  <axis xyz="-1.0 -0.0 -0.0"/>
  <limit upper="0.523599" lower="-1.570796" effort="100" velocity="100"/>
</joint>

<joint name="L_thigh" type="revolute">
  <origin xyz="0.024 -0.024 -0.083" rpy="0 0 0"/>
  <parent link="L_hip_joint_1"/>
  <child link="L_thigh_1"/>
  <axis xyz="0.0 -1.0 -0.0"/>
  <limit upper="2.356194" lower="-2.356194" effort="100" velocity="100"/>
</joint>

<joint name="L_knee" type="revolute">
  <origin xyz="0.0 0.0 -0.076783" rpy="0 0 0"/>
  <parent link="L_thigh_1"/>
  <child link="L_knee_1"/>
  <axis xyz="0.0 -1.0 -0.0"/>
  <limit upper="1.570796" lower="-2.356194" effort="100" velocity="100"/>
</joint>

<joint name="L_ankle_pitch" type="revolute">
  <origin xyz="0.022174 0.0 -0.059681" rpy="0 0 0"/>
  <parent link="L_knee_1"/>
  <child link="L_ankle_pitch_1"/>
  <axis xyz="-0.0 -1.0 0.0"/>
  <limit upper="1.570796" lower="-0.698132" effort="100" velocity="100"/>
</joint>

<joint name="L_ankle_roll" type="revolute">
  <origin xyz="-0.033391 0.014 -0.044187" rpy="0 0 0"/>
  <parent link="L_ankle_pitch_1"/>
  <child link="L_ankle_roll_1"/>
  <axis xyz="-1.0 -0.0 -0.0"/>
  <limit upper="1.570796" lower="-0.523599" effort="100" velocity="100"/>
</joint>

<joint name="R_hip_joint" type="revolute">
  <origin xyz="-0.03132 -0.046412 0.280792" rpy="0 0 0"/>
  <parent link="base_link"/>
  <child link="R_hip_joint_1"/>
  <axis xyz="-1.0 -0.0 -0.0"/>
  <limit upper="1.570796" lower="-0.523599" effort="100" velocity="100"/>
</joint>

<joint name="R_thigh" type="revolute">
  <origin xyz="0.024 0.024 -0.083" rpy="0 0 0"/>
  <parent link="R_hip_joint_1"/>
  <child link="R_thigh_1"/>
  <axis xyz="-0.0 1.0 0.0"/>
  <limit upper="2.356194" lower="-2.356194" effort="100" velocity="100"/>
</joint>

<joint name="R_knee" type="revolute">
  <origin xyz="0.0 0.0 -0.076783" rpy="0 0 0"/>
  <parent link="R_thigh_1"/>
  <child link="R_knee_1"/>
  <axis xyz="0.0 1.0 0.0"/>
  <limit upper="2.356194" lower="-1.570796" effort="100" velocity="100"/>
</joint>

<joint name="R_ankle_pitch" type="revolute">
  <origin xyz="0.022174 0.0 -0.059681" rpy="0 0 0"/>
  <parent link="R_knee_1"/>
  <child link="R_ankle_pitch_1"/>
  <axis xyz="-0.0 1.0 0.0"/>
  <limit upper="0.698132" lower="-1.570796" effort="100" velocity="100"/>
</joint>

<joint name="R_ankle_roll" type="revolute">
  <origin xyz="-0.033391 -0.014 -0.044187" rpy="0 0 0"/>
  <parent link="R_ankle_pitch_1"/>
  <child link="R_ankle_roll_1"/>
  <axis xyz="-1.0 -0.0 -0.0"/>
  <limit upper="0.523599" lower="-1.570796" effort="100" velocity="100"/>
</joint>

<joint name="L_shoulder_joint" type="revolute">
  <origin xyz="-0.017934 0.06728 0.365021" rpy="0 0 0"/>
  <parent link="base_link"/>
  <child link="L_shoulder_joint_1"/>
  <axis xyz="-0.0 1.0 0.0"/>
  <limit upper="3.141593" lower="-3.141593" effort="100" velocity="100"/>
</joint>

<joint name="L_upperarm" type="revolute">
  <origin xyz="-0.024 0.031681 0.022174" rpy="0 0 0"/>
  <parent link="L_shoulder_joint_1"/>
  <child link="L_upperarm_1"/>
  <axis xyz="-1.0 -0.0 0.0"/>
  <limit upper="0.174533" lower="-3.752458" effort="100" velocity="100"/>
</joint>

<joint name="L_forearm" type="revolute">
  <origin xyz="0.0005 0.000187 -0.094392" rpy="0 0 0"/>
  <parent link="L_upperarm_1"/>
  <child link="L_forearm_1"/>
  <axis xyz="-1.0 0.0 0.0"/>
  <limit upper="3.141593" lower="-2.443461" effort="100" velocity="100"/>
</joint>

<joint name="R_shoulder_joint" type="revolute">
  <origin xyz="-0.017928 -0.07182 0.365021" rpy="0 0 0"/>
  <parent link="base_link"/>
  <child link="R_shoulder_joint_1"/>
  <axis xyz="0.0 -1.0 0.0"/>
  <limit upper="3.141593" lower="-3.141593" effort="100" velocity="100"/>
</joint>
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

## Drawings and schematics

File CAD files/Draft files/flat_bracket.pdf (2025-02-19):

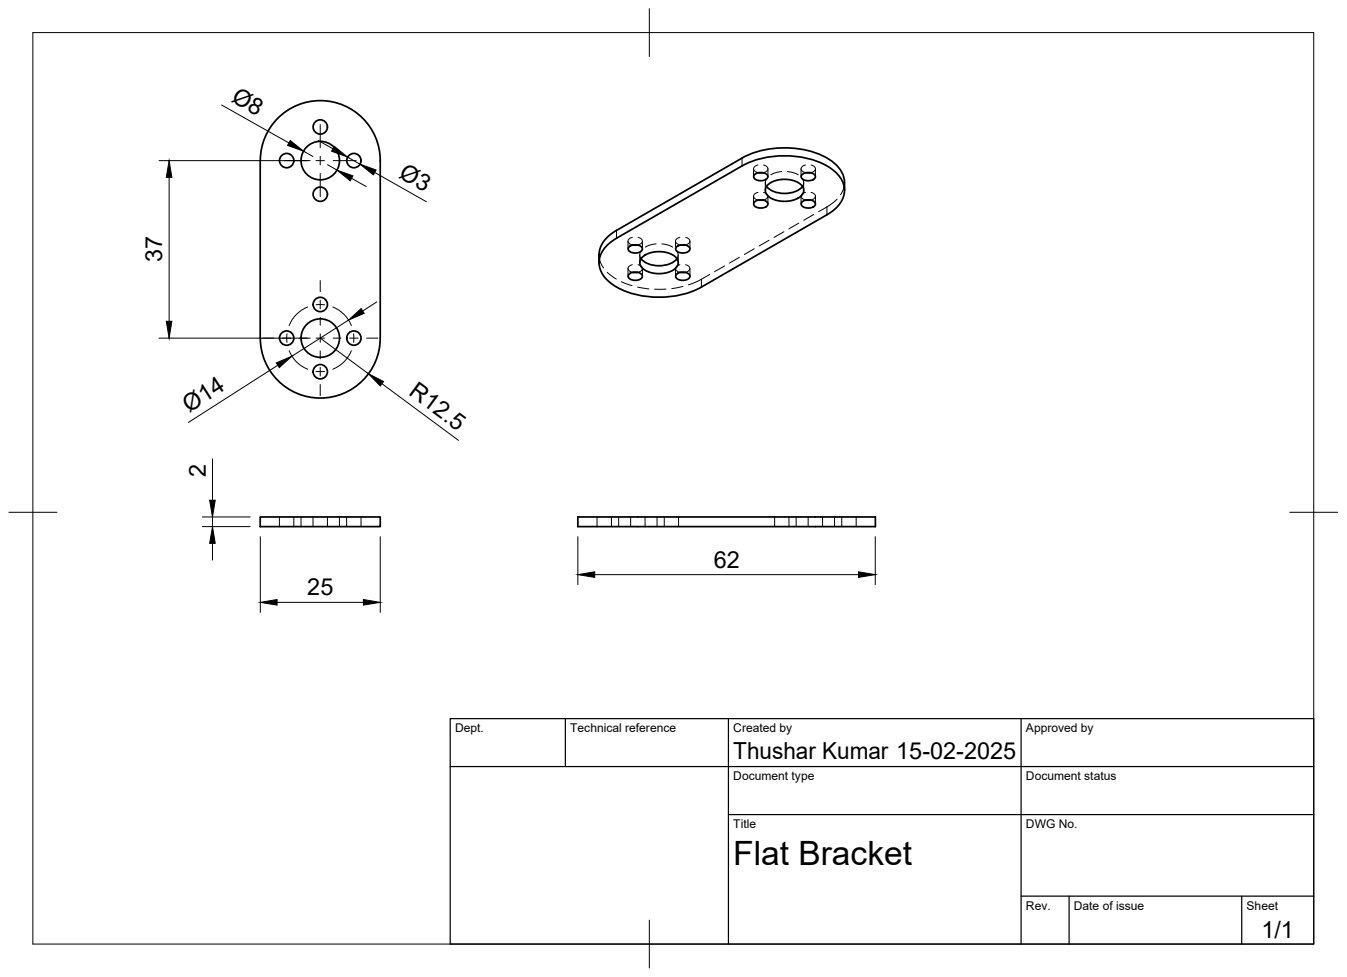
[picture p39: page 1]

Dept. | Technical reference | Created by Thushar Kumar 15-02-2025 | Approved by

Document type | Document status

Title Flat Bracket | DWG No.

Rev. | Date of issue | Sheet 1/1

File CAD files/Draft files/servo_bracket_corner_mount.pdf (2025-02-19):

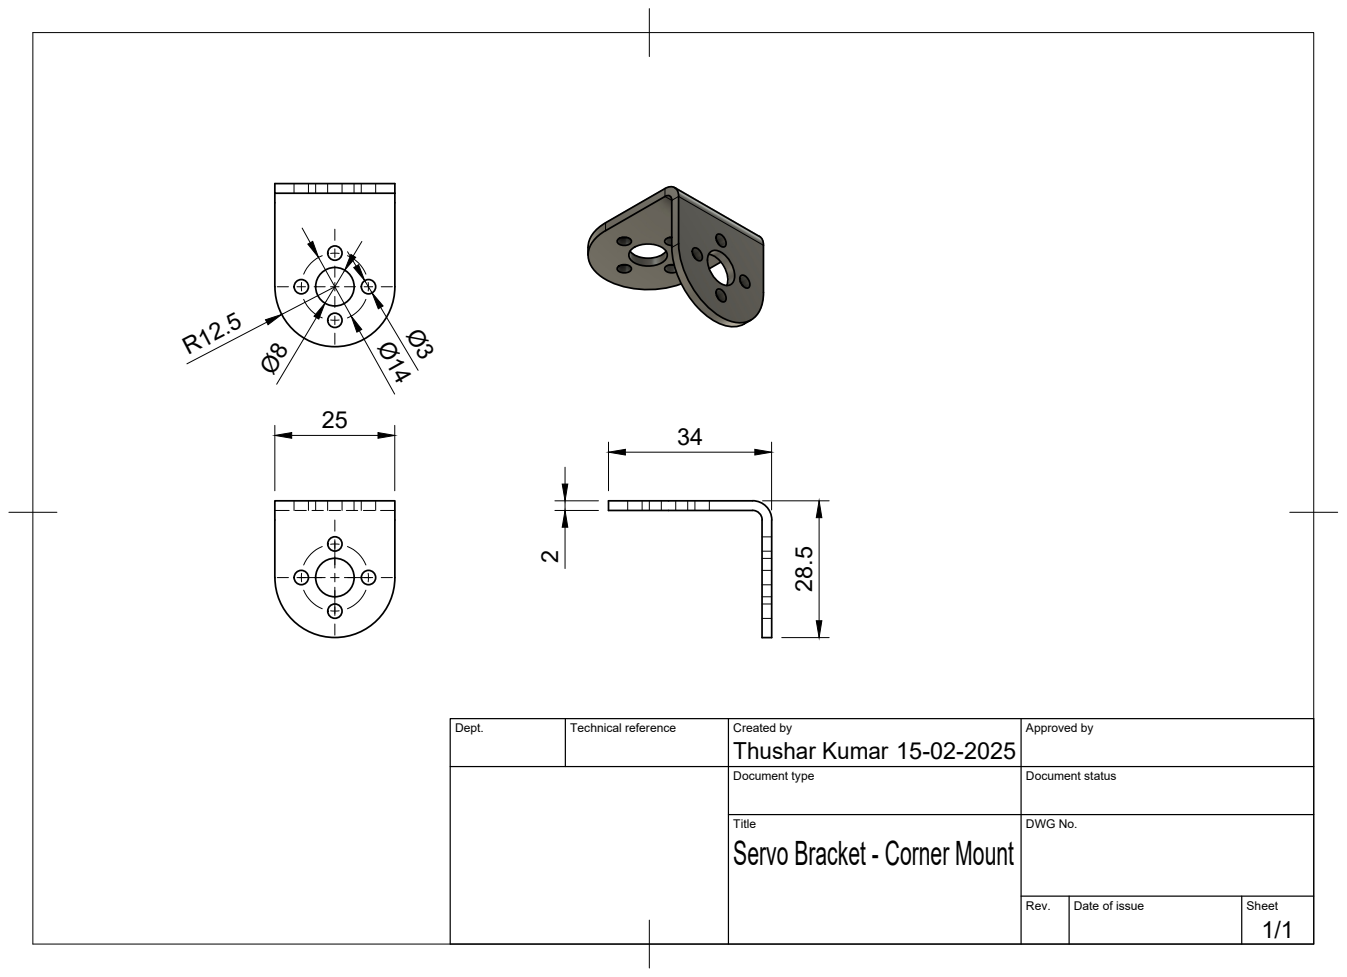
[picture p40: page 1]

Dept. | Technical reference | Created by Thushar Kumar 15-02-2025 | Approved by

Document type | Document status

Title Servo Bracket - Corner Mount | DWG No.

Rev. | Date of issue | Sheet 1/1

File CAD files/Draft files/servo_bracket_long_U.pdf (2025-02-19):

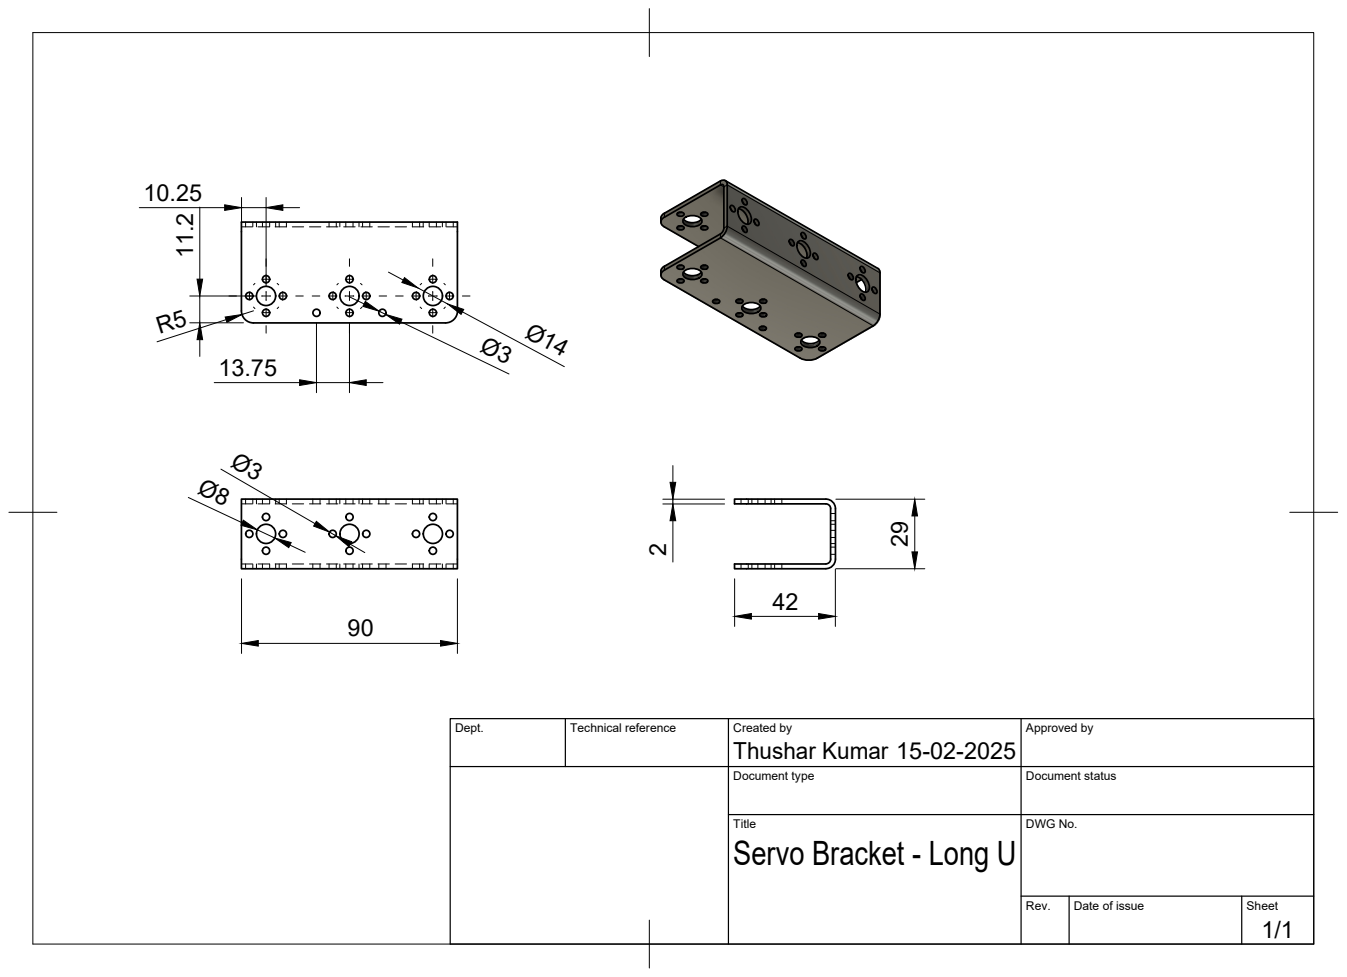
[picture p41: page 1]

Dept. | Technical reference | Created by Thushar Kumar 15-02-2025 | Approved by

Document type | Document status

Title Servo Bracket - Long U | DWG No.

Rev. | Date of issue | Sheet 1/1

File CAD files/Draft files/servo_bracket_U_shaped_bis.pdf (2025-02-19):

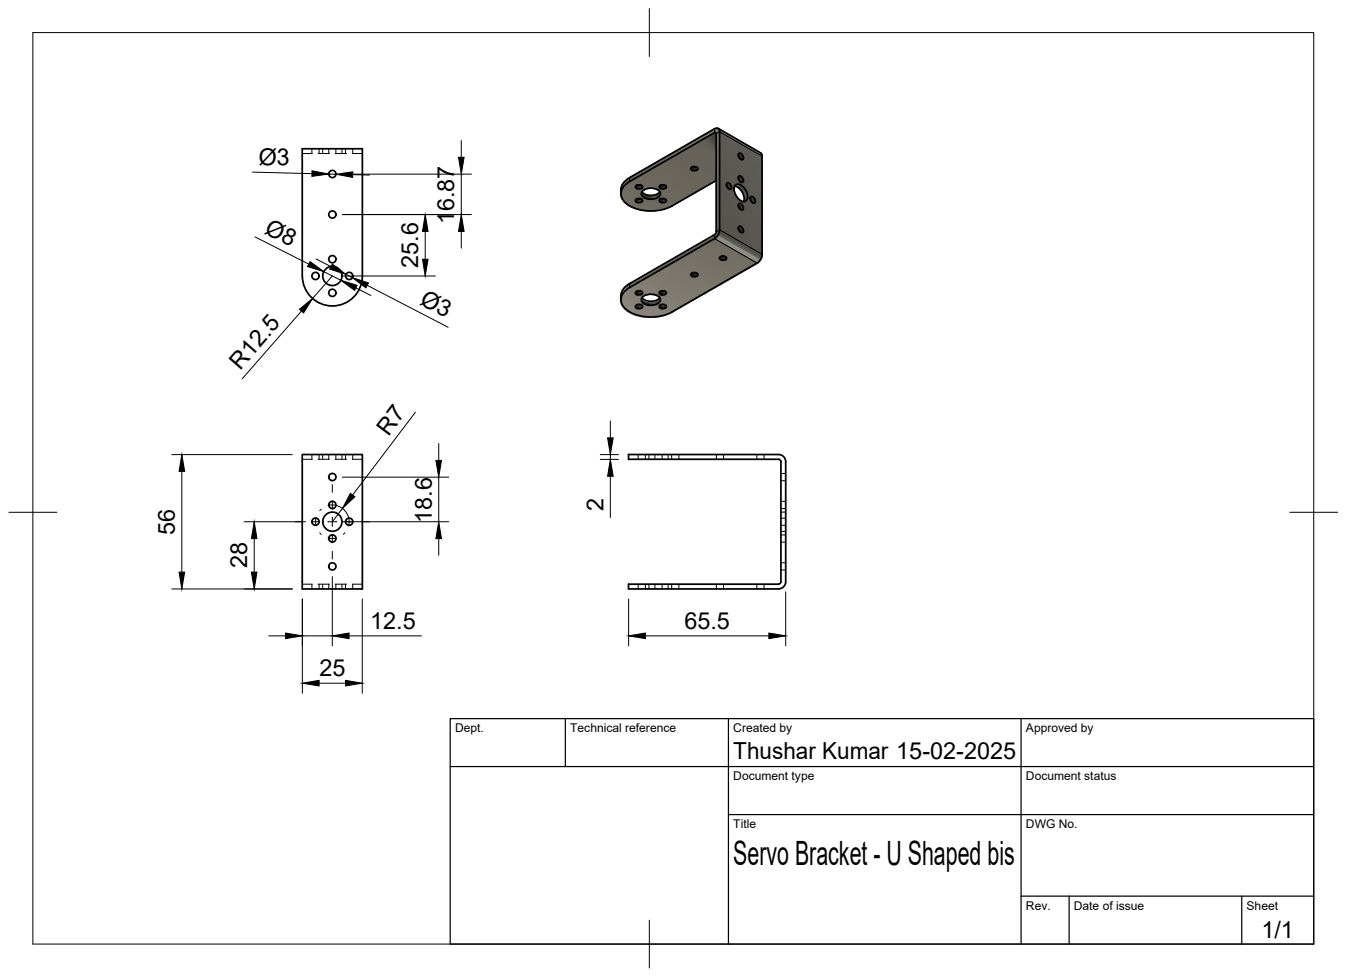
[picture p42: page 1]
Thushar Kumar 56

Dept. | Technical reference | Created by 15-02-2025 | Approved by

Document type | Document status

Title Servo Bracket - U Shaped bis | DWG No.

Rev. | Date of issue | Sheet 1/1

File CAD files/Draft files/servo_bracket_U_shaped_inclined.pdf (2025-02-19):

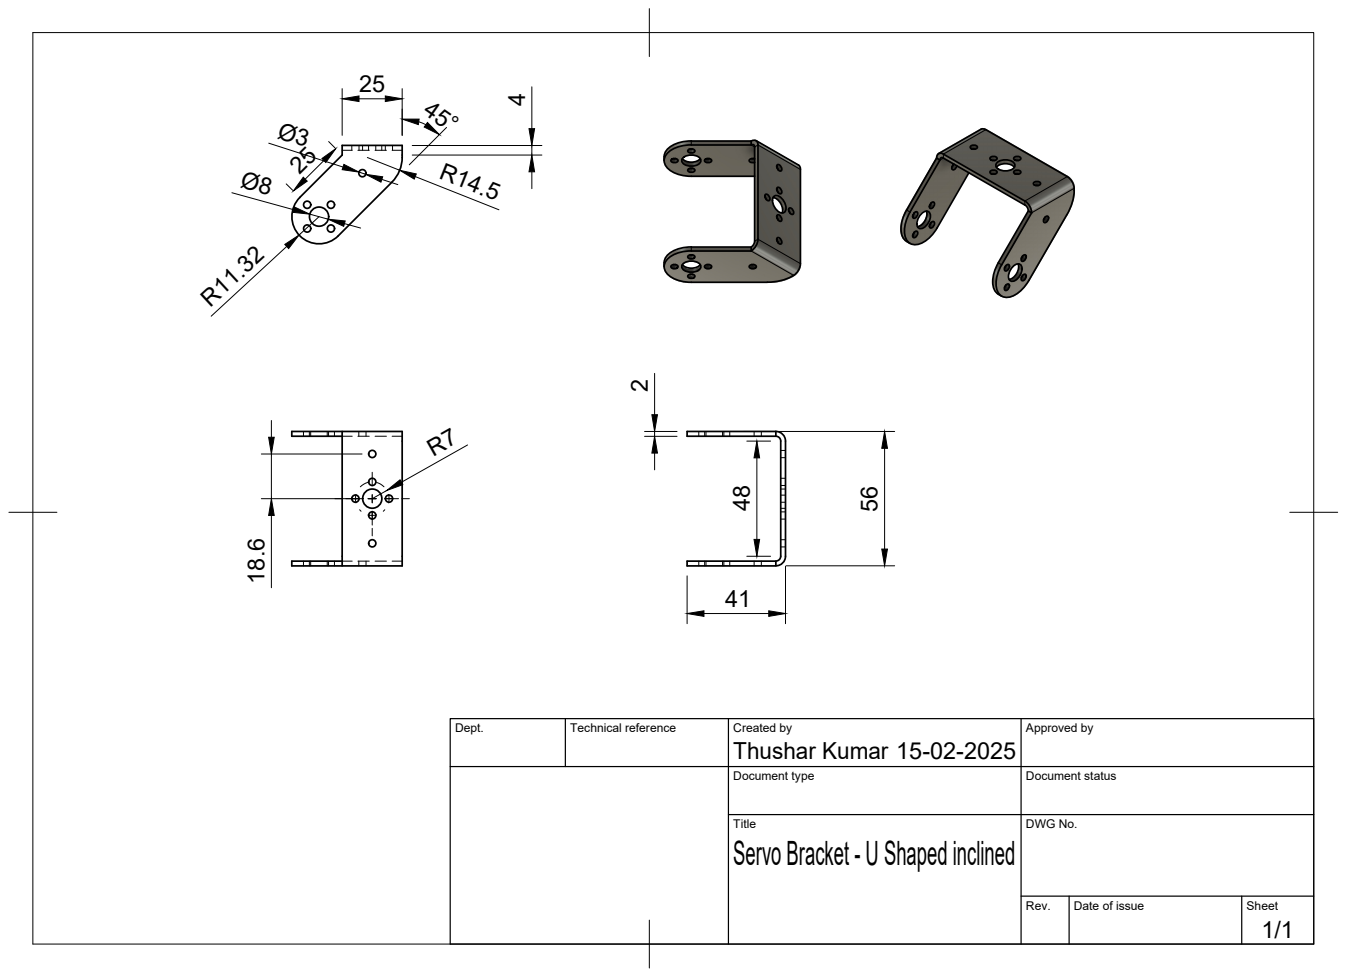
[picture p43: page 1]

Dept. | Technical reference | Created by Thushar Kumar 15-02-2025 | Approved by

Document type | Document status

Title Servo Bracket - U Shaped inclined | DWG No.

Rev. | Date of issue | Sheet 1/1

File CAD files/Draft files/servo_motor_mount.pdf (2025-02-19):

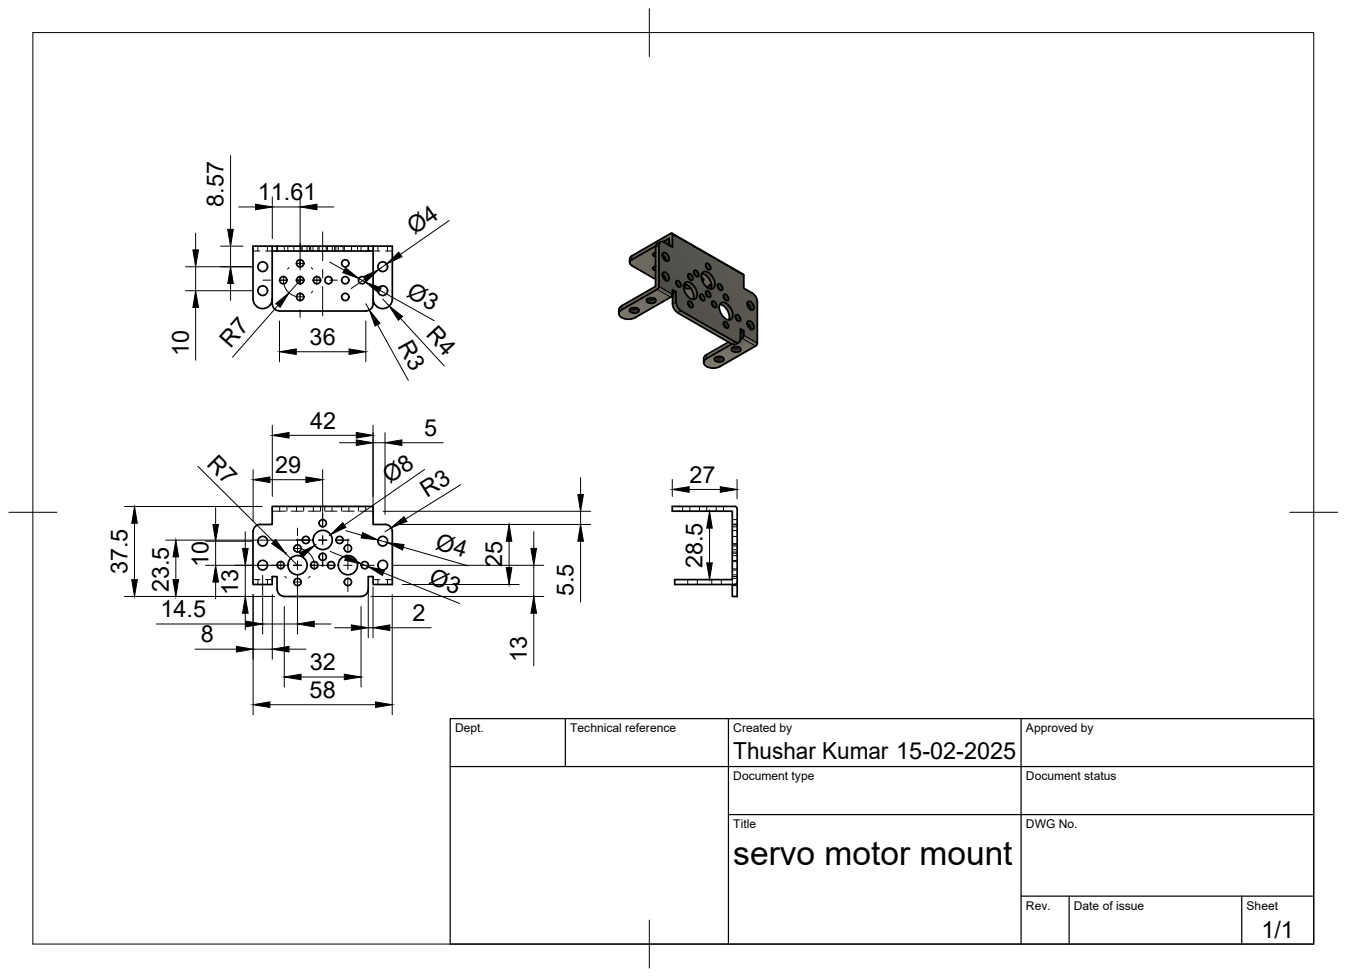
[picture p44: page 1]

Dept. | Technical reference | Created by Thushar Kumar 15-02-2025 | Approved by

Document type | Document status

Title servo motor mount | DWG No.

Rev. | Date of issue | Sheet 1/1

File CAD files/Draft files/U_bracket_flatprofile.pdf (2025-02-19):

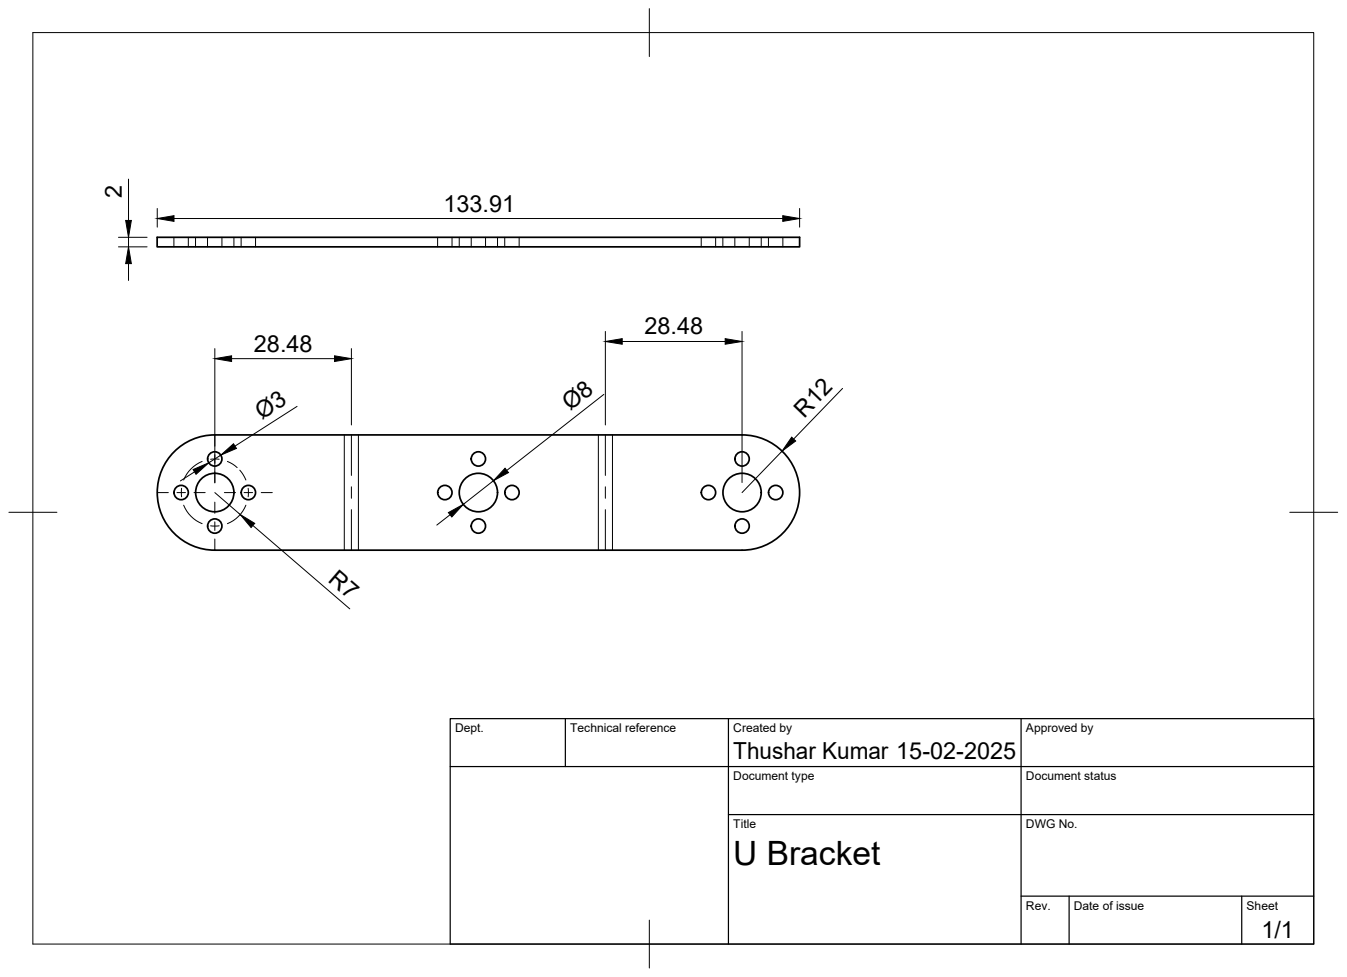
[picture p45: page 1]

Dept. | Technical reference | Created by Thushar Kumar 15-02-2025 | Approved by

Document type | Document status

Title U Bracket | DWG No.

Rev. | Date of issue | Sheet 1/1

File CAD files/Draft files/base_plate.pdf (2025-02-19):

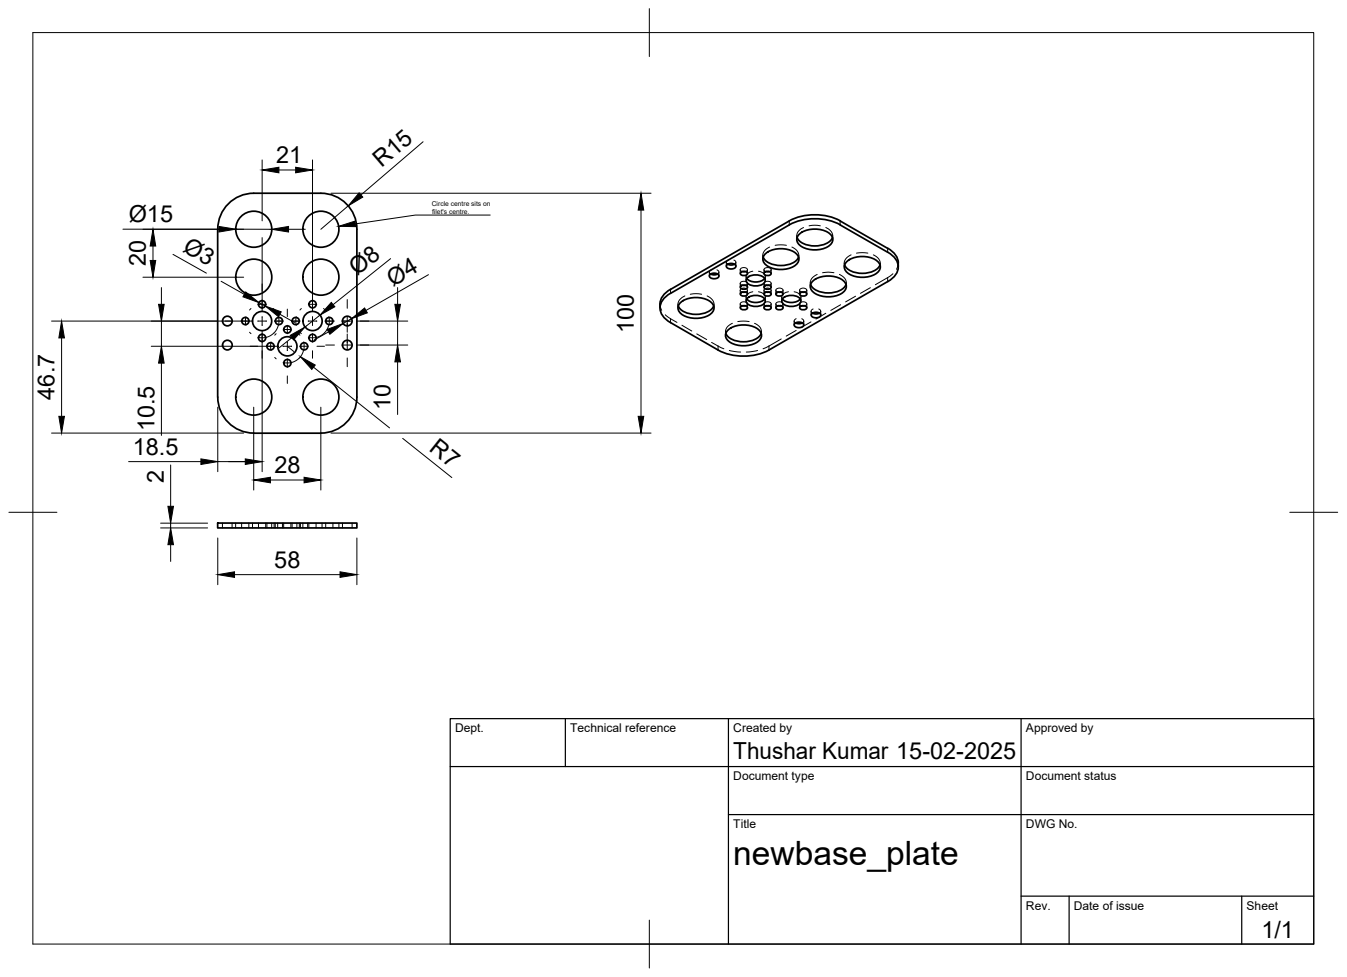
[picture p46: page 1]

Circle centre sits on
filet's centre.

Dept. | Technical reference | Created by Thushar Kumar 15-02-2025 | Approved by

Document type | Document status

Title newbase_plate | DWG No.

Rev. | Date of issue | Sheet 1/1

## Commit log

2025-02-19 added folder
    [Head_1.stl, L_ankle_pitch_1.stl, L_ankle_roll_1.stl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]
2025-02-19 uploaded folder
    [Head_1.stl, L_ankle_pitch_1.stl, L_ankle_roll_1.stl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]
2025-02-21 Updated package
    [humanoid.xacro, humanoid_control.xacro, humanoid_controllers.yaml]
